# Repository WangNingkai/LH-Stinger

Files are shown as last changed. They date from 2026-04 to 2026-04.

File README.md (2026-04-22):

<p align="center">
  <p align="center">
   
  </p>
	<h1 align="center"><b>LH Stinger</b></h1>
	<p align="center"> <strong>
		A no-compromise cartesian 3D Printer designed for speed and precision, created as a long-lasting platform for those who like to push quality and speed to the extreme.  </strong>
    <br />
    <br />
        <br />
    <i>~ A community-driven project ~ </i>
    <br /> 
    <br />
      
    <br />
</a>
  </p>
</p>

<br>

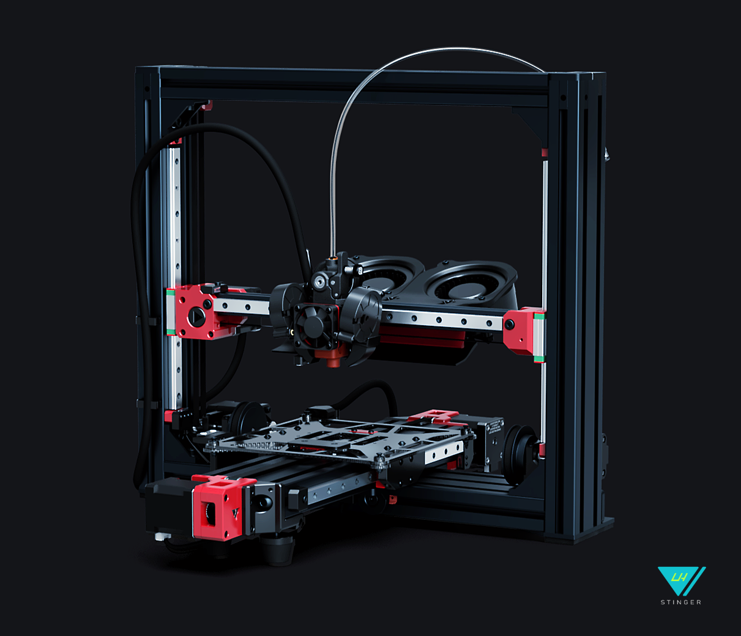
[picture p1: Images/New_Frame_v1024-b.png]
Image of LH Stinger 3D Printer Front View
  

<br>

  
Status: **V1.0**  

<br>

## Sponsors

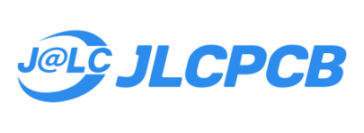
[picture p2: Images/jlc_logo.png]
JLCPCB (https://flexheater.jlcpcb.com/?from=LH_STINGER)

  
   Sponsored by [JLCPCB Flexible Heaters](https://flexheater.jlcpcb.com/?from=LH_STINGER) - **Custom Flex Heaters for Your Build**
<br>

## Contents

- [Features](#features)
- [Kits - BOM](#kits---bom)
- [Resources](#resources)
- [Assembly Instructions](#assembly-instructions)
- [Addons](#addons)
- [Contact](#contact)
- [Credits](#credits)
- [Supporters](#supporters)
- [License](#license)

<br>

## Features
_**(at BOM Spec)**_
<br>

- Cross Frame design focused on stiffness and stability with a low center of gravity
- Streamlined frame assembly consisting of only six extrusions
- Lightweight bed carriage assembly with carbon fiber components
- AWD stepper configuration for the Y-axis
  - Optional conversion for X-axis AWD setup
- 235 x 235 x 200 mm maximum build volume (easily expandable to other sizes)
  - (200 mm)^2 [Carbon Fiber Bed](/DXF) for high-speed setup
  - (235 mm)^2 bed support for a larger volume
- Optimized for daily print speeds of 400-600 mm/s with 20.000 mm/s^2 acceleration ([Test A](https://www.youtube.com/watch?v=bxNQv3xVFXA&)) ([Test B](https://www.youtube.com/watch?v=mh0rmYptH-0)) ([Test C](https://www.youtube.com/watch?v=cDipS-Msi5c))
- Motion system capable of 1.000 mm/s speed with 100.000 mm/s^2 acceleration ([Test](https://www.youtube.com/watch?v=Xajs2mky6ZU))
- Maximum volumetric flow rate: ~55-60 mm^3/s ([Test A](https://www.youtube.com/watch?v=K3M1EXKJzKs)) ([Test B](https://www.youtube.com/shorts/JorOoNuft90))
- Built using 30 series T-slotted extrusions with parts up to 3090
- All bracket assembly
- Genuine high-quality motion system components ([BOM](https://docs.google.com/spreadsheets/d/1s8ulLfThmbuy1G_40MvkXXL2oVx9PZhvpAY9hMxqYbg/edit?usp=drive_link))
- Entire motion system based on high preload MGN12H linear guide rails
- Fully belt-driven with minimal belt paths
- 9mm 2GT belt in symmetrical configuration for the Y-axis
- 6mm 2GT belts for the rest of the axis
- Independent Z stepper motors with Z Tilt capability for the X-axis
- Lightweight dual plate [Carbon Fiber Bed Carriage](/DXF) with integrated tensioner and compatible with different bed sizes and carriage configurations
- Rigid carbon fiber bed mount
- Lightweight Polyimide flex PCB 200W [Bed Heater](/PCB/PI%20Bed%20Heater%20-%20200mm)
- Double shear shaft supports for Y and X axis steppers
- High torque LDO-42STH48-2504AC stepper motors supplied with 36V for the X and Y-axis
- Dual power supply supporting 24V and 36V power standards (easily configurable for 48V)
- Driven by the Octopus Pro 1.1 board with TMC2240 drivers
- Running [Klipper](https://github.com/Klipper3d/klipper)/[Kalico](https://github.com/KalicoCrew/kalico) firmware
- Fully featured Klipper [Configuration](/Config/Klipper_Config) and [Slicer Profiles](/Config/Orca_Slicer) available
- Easily serviceable [External electronic box](https://github.com/lhndo/LH-Stinger/wiki/Build-Log#electronic-box-design) with good airflow, and support for multiple power supplies, SSRs, RPi and large controller boards.
- Good cable management with a quick disconnect [Breakout Board](/PCB/LHS%20Breakbeat) between the printer and ebox
- Toolhead based on the Dragon HF hotend and HF extender
  - Alternate hotends supported: Dragon UHF, Ace, Mellow NF-Crazy-Volcano HF, Rapido, Goliath ([User Mods](/User_Mods/Toolhead/))
- LDO Orbiter 2.5 direct drive extruder
  - Sherpa Mini supported ([User Mods](/User_Mods/Printer))
- Dual 5015 fan setup for part cooling
- Dual [AUX cooling modules](/CAD/Aux%20Fan) based on 9733 blower fans providing 64 CFM of auxiliary cooling
- Adopts the [Annex Engineering Quickdraw Probe](https://github.com/Annex-Engineering/Quickdraw_Probe)
	- Zero Y offset probe placement for no gantry twist deviation
	- Full bed probe coverage
- Minimalistic [printed part design](/STL) focused on strength and easy printability
- Printed in ASA, providing high temperature resistance
- Easily enclosed, with the main electronic components outside of the build chamber.
  - The (200 mm)^2 bed configuration can be fully enclose up to the frame bounding box, with no extra space needed for the bed movement. ([Dimensions](https://github.com/lhndo/LH-Stinger/wiki/Dimensions))

<br>

**Resonance Tests:**<br>
Resonance Test X<br>
Resonance Test Y<br>

<br>

## Kits - BOM

* This project can be self-sourced by following the [**BOM Guide**](https://docs.google.com/spreadsheets/d/1s8ulLfThmbuy1G_40MvkXXL2oVx9PZhvpAY9hMxqYbg/).  

* An official upgraded **LH Stinger - Rev2 Kit** is produced and sold by **[FYSETC](https://www.fysetc.com/products/lh-stinger-3d-printer-kit)**.

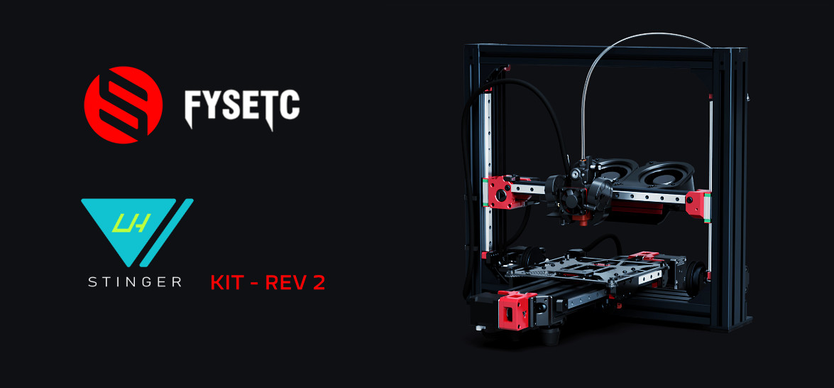
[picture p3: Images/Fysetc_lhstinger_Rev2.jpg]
Fysetc LH Stinger Rev2 Kit (https://www.fysetc.com/products/lh-stinger-3d-printer-kit)
<br>

### Kit Highlights:

* Phaetus Dragon UHF - Hotend
* FYSETC Sherpa Mini - All Metal - CNC Extruder
* MGN 12H Z1 Preload Linear Rails
* FYSETC Spider V3.0 H7 (550Mhz) High Voltage board 
* 48V Power with TMC5160 Drivers (AWD Y, X Axis)
* High Torque 2.5A 580mN.m Stepper Motors with 30mm shafts for double shear support
* Delta (48V) and Meanwell (24V) PSUs
* Carbon Fiber Bed with Pre-applied PI Heater and Pre-epoxied CF Carriage Assembly
* LHS Breakbeat distribution board and wiring harness

**You require**: The **Printed Parts** and a **BTT Pi V1.2** or **Raspberry Pi** SBC (Klipper Host)
<br>

[**Fysetc - LH Stinger - Kit**](https://www.fysetc.com/products/lh-stinger-3d-printer-kit)  
  
Use the code **FYSBKSALELH** for a total of **$699**. Free shipping directly from US/EU.  
A portion of every kit sale goes towards supporting the project! :purple_heart:  

<br>

## Resources
<br>

- [**Assembly Guide**](https://github.com/lhndo/LH-Stinger/wiki/)
- [STL Files and Printing Instructions](STL/)  
- [CAD Source Files ](CAD/)
- [Klipper Configuration ](Config/Klipper_Config) 
- [Build Log](https://github.com/lhndo/LH-Stinger/wiki/Build-Log)
- [Videos](https://www.youtube.com/channel/UCPD2Ai4b49gVoCFSGFWoSdw) 

<br>

## Assembly Instructions 

* The [LH Stinger Wiki](https://github.com/lhndo/LH-Stinger/wiki) is a regularly updated and intended to serve as your primary point of reference during the build  

* The main body of documentation can be found in the [**Assembly Guide**](https://github.com/lhndo/LH-Stinger/wiki/Assembly-Guide)  

<br>

*For additional support please join us on the [LH Stinger Discord](https://discord.gg/EzssCfnEDS)*

<br>

## Addons

- [**LHS Pico MMU**](https://github.com/lhndo/LH-Stinger/wiki/Pico-MMU)  

LH Stinger - LHS - Pico MMU

- **Enclosure** *(In progress)* 
  *by zwirbel*

<br>

LH Stinger Enclosure  

<br>

- An extensive range of [**community mods**]((/User_Mods)) available

<br>

## Contact

lemurshaze @ gmail.com  
@LH on [LH Stinger Discord](https://discord.gg/EzssCfnEDS)
<br>

## Credits

<br>

**Thanks to everyone in the LH Stinger community who supported the project, contributed in any form, or provided feedback! :purple_heart:**

<br>

_Inspired by the [Annex Engineering](https://github.com/Annex-Engineering) team and [community](https://discord.com/invite/MzTR3zE), along with the [Klipper community](https://discord.klipper3d.org), [RatRig](https://ratrig.com/) and all the crazy people that continue to push bed slingers to their limits. :purple_heart:_

-Toolhead evolved from an amazing design by [Dalegaard](https://github.com/dalegaard)  
-Silicon sock mold based on [Renátó Kulman](https://www.printables.com/@RenatoKulman)  
-Wago 221 mounts by [fns720](https://www.printables.com/@fns720)  
-SSR protection cover based on [Technoturk](https://www.printables.com/@Technoturk_377911)  
-3030 extrusion Cable clip based on [Arthur_C](https://www.printables.com/@Arthur_C_428094)  
-3030 t-nut clip based on [John_S](https://www.printables.com/@JohnS)  
<br>

## Supporters

<br>

*Special thanks to those who donated to this project throughout its development!* :purple_heart:  

**djezo888. Fen, Budz, techb0i, PinGZ, abstractFlo, BeccaK, Steven @crydteam, Robin @crydteam, Fred Bernton, Mawoka, rmxbit, Mcclane, malar6606, EMMY BEAR 3D, Killa_Prints, Michel, vr6deezy, Ajax240, Zemlos01, popster, Dan, Sibert, Ultracopa, yoske, Arjun, iKuro**  

If you would like to give your support, please use the link below:



<br>

## License

This work is licensed under a [Creative Commons (4.0 International License)  ](https://creativecommons.org/licenses/by-nc-sa/4.0/)  
[**Attribution—Noncommercial—Share Alike**](LICENSE.md)  

[][cc-by-nc-sa] [][l2] [][l5] 

[s1]: https://img.shields.io/badge/Buy%20Me%20a%20Coffeee-d3dsds?logo=ko-fi&logoColor=white&labelColor=red&color=red
[l1]: https://ko-fi.com/lh_eng
[s2]: https://img.shields.io/badge/Discord-asdsadsa?logo=discord&logoColor=white&color=5865F2
[l2]: https://discord.gg/EzssCfnEDS
[s5]: https://img.shields.io/badge/Youtube-8A2323443?logo=youtube&logoColor=red&color=white
[l5]: https://www.youtube.com/@LemurHaze

[cc-by-nc-sa]: http://creativecommons.org/licenses/by-nc-sa/4.0/
[cc-by-nc-sa-image]: https://licensebuttons.net/l/by-nc-sa/4.0/88x31.png
[cc-by-nc-sa-shield]: https://img.shields.io/badge/License-CC%20BY--NC--SA%204.0-lightgrey.svg

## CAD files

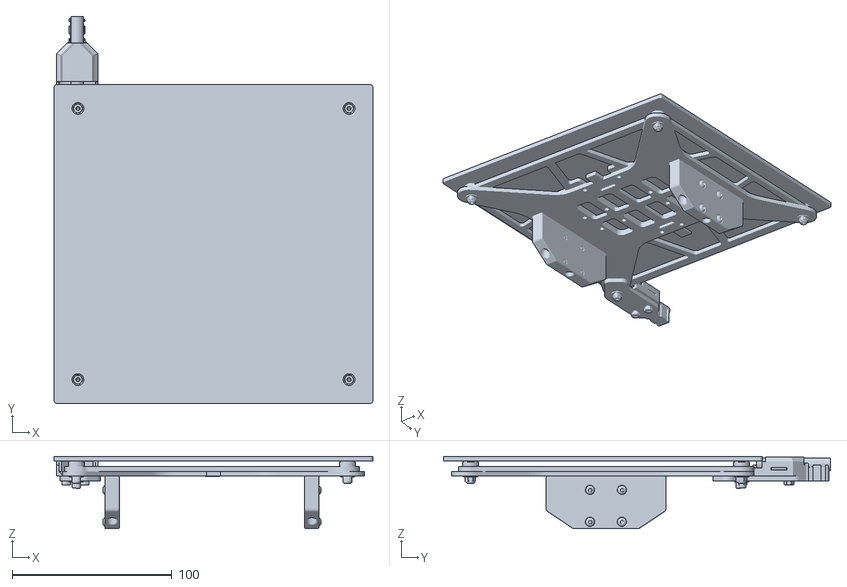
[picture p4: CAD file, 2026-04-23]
Config/Orca_Slicer/LH Stinger 200 Bed Model.stl
200.0 x 242.7 x 45.4

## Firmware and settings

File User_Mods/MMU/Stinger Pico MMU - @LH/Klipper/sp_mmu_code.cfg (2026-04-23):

### Do not edit or include this file into printer.cfg
### VERSION: 1.0.5
### REQUIRES CONFIGURATION TEMPLATE VERSION: 0.9.4

###_______________  LH STINGER PICO MMU  _____________________
### https://github.com/lhndo/LH-Stinger/wiki/Pico-MMU
### This code is licensed under a Creative Commons (4.0 International License)Attribution—Noncommercial—Share Alike




#### ------ BOOT INIT ----------


[delayed_gcode _SP_BOOT]
initial_duration: 3
gcode:
  {% set sp = printer['gcode_macro _SP_VARS'] %}
  {% set loaded_lane = printer.save_variables.variables.last_loaded_lane | default(-2) | int %}
 
  {% if sp.enabled == 1 %}
    RESPOND MSG="---- LH Stinger Pico MMU Enabled ----"
    RESPOND MSG=""

    {% if sp.sync_mode >= 1 %}
      RESPOND MSG="SP: Alt Klipper Sync Mode Enabled"
      {% if printer.configfile.settings.extruder.min_extrude_temp|int >= 20 %}
        RESPOND TYPE=error MSG="SP: Please set [extruder] min_extrude_temp and min_temp to 0 in your printer.cfg !"
      {% endif %}
    {% endif %}

    {% if loaded_lane >= 0 %}
      RESPOND MSG="SP: Loaded Extruder Lane saved: {printer.save_variables.variables.last_loaded_lane}"
    {% else %}
      RESPOND MSG="SP: No loaded LANE saved in memory"
    {% endif %}
    
    RESPOND MSG="SP: Initializing LH Stinger Pico MMU"
    {% if sp.has_guest_lane == 1 %} 
      SET_GCODE_VARIABLE MACRO=_SP_VARS VARIABLE=lanes VALUE={sp.lanes + 1}  ## extending the number of lanes to include the guest lane
    {% endif %}
    _SP_NOTIFY ACTION="boot" 
    _SP_REFRESH_STATE
    SP_INIT
    _CHECK_SETTINGS_VERSION_SP
  
  {% else %}
    RESPOND MSG="---- LH Stinger Pico MMU Disabled ----"
    SET_FILAMENT_SENSOR SENSOR=sp_sensor_runout ENABLE=0
  {% endif %}



[gcode_macro SP_INIT]
gcode:
  {% set sp = printer['gcode_macro _SP_VARS'] %}
  {% set rt = printer['gcode_macro _SP_VARS_RUNTIME'] %}
  {% set loaded_lane = printer.save_variables.variables.last_loaded_lane | default(-2) | int %}
  RESPOND MSG="SP: Initializing Pico MMU"
  SET_FILAMENT_SENSOR SENSOR=sp_sensor_runout ENABLE=0
  SET_GCODE_VARIABLE MACRO=_SP_VARS_RUNTIME VARIABLE=fused VALUE=0
  SET_GCODE_VARIABLE MACRO=_SP_VARS_RUNTIME VARIABLE=next_purge VALUE={sp.print_start_change_purge} ## Setting the purge amount to the user set value
  
  {% if rt.is_filament_in == 1 %}
    RESPOND MSG="SP: Inserted filament detected"

    {% if loaded_lane < 0 %}
      RESPOND MSG="SP: WARNING! Unknown LANE loaded! Please verify your system and use SP_FORCE_SET_LOADED_LANE LANE=<0...> to manually set the loaded lane"
      RESPOND MSG="SP: WARNING! Defaulting to LANE 0! Please correct if not accurate!"
      _SP_UI_MSG MSG="Unknown LANE loaded!  Defaulting to LANE 0.  Please correct if not accurate" TITLE="WARNING"
      _SP_SET_LOADED_LANE LANE=0
      SAVE_VARIABLE VARIABLE=hotend_loaded VALUE=1
      _SP_NOTIFY ACTION="loaded" LANE=0 COMPLETE=1 ERROR=1 
    {% else %}
      RESPOND MSG="SP: >>>> Loaded LANE {printer.save_variables.variables.last_loaded_lane} <<<< "  
      _SP_NOTIFY ACTION="loaded" LANE={printer.save_variables.variables.last_loaded_lane} COMPLETE=1
    {% endif %}

  {% else %}
      {% if printer.save_variables.variables.last_loaded_lane != -1  %}
        RESPOND MSG="SP: WARNING! Last set LANE was {printer.save_variables.variables.last_loaded_lane}, but no filament is detected! Resetting lane memory"
      {% endif %}

      _SP_SET_LOADED_LANE LANE=-1
      SAVE_VARIABLE VARIABLE=hotend_loaded VALUE=0
      SET_GCODE_VARIABLE MACRO=_SP_VARS_RUNTIME VARIABLE=is_filament_in VALUE=0
      RESPOND MSG="SP: Filament not present in the hotend"             
  {% endif %}

  SP_HOME
  SP_CLEAR_ERROR_CODES 
  _SP_RESET_VARIABLES
  _SP_REFRESH_STATE



### The macro below is broken into A B parts to obtain refreshed variables for error checking
[gcode_macro _SP_PRINT_START]
gcode:
  {% set lane = params.LANE| default(-1) | int %}
  {% set temp = params.TEMP| default(0) | int %}
  {% set no_start_purge = params.NO_START_PURGE | default(0) | int %}
  {% set unload_lane = printer.save_variables.variables.last_loaded_lane | default(-1) | int %}
  {% set sp = printer['gcode_macro _SP_VARS'] %}
  {% set rt = printer['gcode_macro _SP_VARS_RUNTIME'] %}
  {% set purge_amount = sp.print_start_change_purge if no_start_purge == 0 else 0 %}

  CLEAR_PAUSE
   
  {% if sp.enabled == 1  %}
    RESPOND MSG="SP: Print Start - Resetting the SP MMU"    
    _SP_REFRESH_STATE
    SP_INIT
    SET_GCODE_VARIABLE MACRO=_SP_VARS_RUNTIME VARIABLE=fused VALUE=1
  
    {% if lane+1 <= sp.lanes and lane >= 0 %}
   
      {% if lane != unload_lane %}        
        RESPOND MSG="SP: ----- Filament Change: LANE {unload_lane} >>>> LANE {lane} ----- "
        SET_GCODE_VARIABLE MACRO=_SP_VARS_RUNTIME VARIABLE=print_start_change VALUE=1

        # Park
        M400
        {% if sp.use_park == 1 and sp.skip_first_park == 0 %}
          _SP_CONDITIONAL_HOME
          _SP_PAUSE_PARK
        {% endif %} 

        ## User Macro Before Change
        M400
        {% if rt.user_macros_executed == 0 %} # if user macro can be executed
          RESPOND MSG="SP: Running User BEFORE_CHANGE Macro"
          SAVE_GCODE_STATE NAME=user_macro
          _SP_BEFORE_CHANGE PRINT_START=1
          M400
          SET_GCODE_VARIABLE MACRO=_SP_VARS_RUNTIME VARIABLE=user_macros_executed VALUE=1
          RESTORE_GCODE_STATE NAME=user_macro
        {% endif %}
 
        ### Filament Change Routine 
        _SP_FILAMENT_CHANGE UNLOAD_LANE={unload_lane} LOAD_LANE={lane} TEMP={temp} PURGE={purge_amount}        
        M400
        _SP_RESTORE_PA FORCE=1
        _SP_REFRESH_STATE
        M400
        _SP_PRINT_START_B


      {% else %}
        RESPOND MSG="SP: No filament change required"             
        RESPOND MSG="SP: Starting print with LANE {lane}"
        SET_FILAMENT_SENSOR SENSOR=sp_sensor_runout ENABLE=1
        SET_GCODE_VARIABLE MACRO=_SP_VARS_RUNTIME VARIABLE=next_purge VALUE=0 ## Setting next purge amount to 0 since no change was required
        SP_CLEAR_ERROR_CODES
      {% endif %}
       
     {% else %}
       RESPOND TYPE=error MSG="SP: ERROR: Invalid LANE inputs. LANE {unload_lane} and loading LANE {lane}"
       _SP_NOTIFY ACTION="empty" COMPLETE=1 ERROR=1 
       _SP_SET_EXIT_CODE CODE=1
     {% endif %}

    _SP_REFRESH_STATE   

  {% else %}
    RESPOND MSG="The SP MMU is not enabled for this print"
  {% endif %}



[gcode_macro _SP_PRINT_START_B]
gcode:
  {% set sp = printer['gcode_macro _SP_VARS'] %}
  {% set rt = printer['gcode_macro _SP_VARS_RUNTIME'] %}
  
  {% if sp.enabled == 1 %}
  
    {% if rt.exit_code == 0 %}

      ## User Macro After Change
      M400
      {% if rt.user_macros_executed == 1 %}
        RESPOND MSG="SP: Running User AFTER_CHANGE Macro"
        SAVE_GCODE_STATE NAME=user_macro
        _SP_AFTER_CHANGE PRINT_START=1
        M400
        RESTORE_GCODE_STATE NAME=user_macro
      {% endif %}  

      RESPOND MSG="SP: Continuing. Please wait"
      RESPOND MSG="SP: Enabling filament runout sensor"
      SET_FILAMENT_SENSOR SENSOR=sp_sensor_runout ENABLE=1
      _SP_REFRESH_STATE
      RESPOND MSG="SP: Turning off hotend before the actual print start"
      M104 S0 # Turn off hotend before the actual print start
      
    {% else %}
      RESPOND TYPE=error MSG="SP: Turning off hotend and PAUSING"
      M104 S0 # Turn off hotend for safety
      SP_HOME
      _SP_NOTIFY ACTION="pause" ERROR=1 
      
      PAUSE
    {% endif %}
    _SP_REFRESH_STATE
    SET_GCODE_VARIABLE MACRO=_SP_VARS_RUNTIME VARIABLE=user_macros_executed VALUE=0  ## Clearing execution even if print start change fails
  {% endif %} 



[gcode_macro _SP_PRINT_END]
gcode:
  RESPOND MSG="SP: ---- Print Ended ----"
  RESPOND MSG="SP: Resetting LH Stinger Pico MMU "
  RESPOND MSG=""
  _SP_NOTIFY ACTION="print_end" 
  _SP_SHOW_STATISTICS
  _SP_REFRESH_STATE
  SP_INIT



### Implementation for RatOS T0 conflict
### The T macros are commented in pico_mmu.cfg
### In Orca Slicer add Change filament G-code: SP_CHANGE T=[next_extruder]
[gcode_macro _SP_CHANGE]
gcode:
  _SP_REFRESH_STATE   
  _SP_TOOL_CHANGE LANE={params.T|int}
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

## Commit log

2026-04-23 tweak position
    [LH Stinger 200 Bed Model.stl]
2026-04-23 Improving messages around disabled/not fused by print start MMU
    [sp_mmu_code.cfg]
